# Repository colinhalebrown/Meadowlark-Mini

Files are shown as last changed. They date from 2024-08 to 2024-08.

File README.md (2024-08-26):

# Meadowlark-Mini

Dual deploy programable flight computer for amature rocketry. Equipt with a beeper, physical interrupt, battery charger/monitoring, ignighter indicators, logging to MicroSD, IMU, and Pressure sensor. The goal is to offer a feature rich contnroller that can fit inside a 29mm chassis with the creature comforts of modern controllers. The system is powered by a onboard RP2040 microcontroller. Running at 125MHz with dual core operation for data collection and flight tracking.  

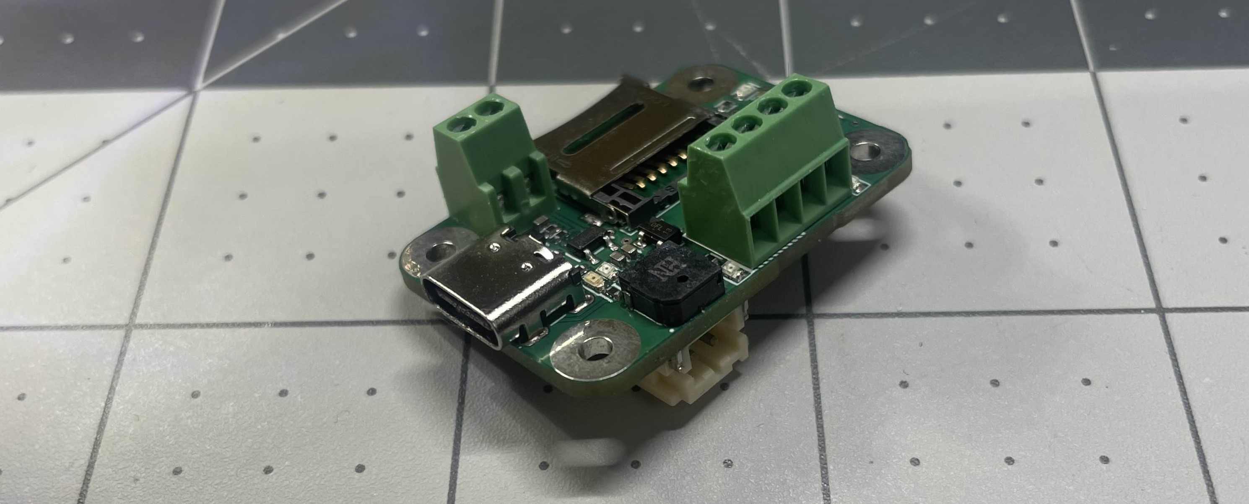
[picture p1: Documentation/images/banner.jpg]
Banner showing PCB


### Hardware Specs
* 260 to 1260 hPa absolute pressure range
* 0.5 hPa absolute pressure accuracy
* +/- 0.025 hPa relative pressure accuracy
* +/- 16g accelerometer range
* +/- 2000 dps gyroscope
* embedded temperature compensation
* 20,000g shock rated
* ~130mA operating consumption 
* Buzzer 80db
* MicroSD data storage

### Hardware Improvements
* add RESET pads for debugging
* move BOOT pads closer together
* Choose different SDcard pins to enable writing code with the picoSDK

### Testing
- [x] Hardware validation
- [x] Firmware Initialized
- [ ] Test Functionallity
        - [x] Indicator light
        - [x] Pyro circuit
        - [x] buzzer
        - [ ] SDcard
        - [ ] Pressure Sensor
        - [ ] IMU
- [ ] Software endurance test
- [ ] Simulated flight test
- [ ] Passeenger flight tests (collect data and tune triggers)
- [ ] Flight as main controller
- [ ] Flight as secondary controller

Repeat any tests until the controller passes with reliable behavior.

# Hardware
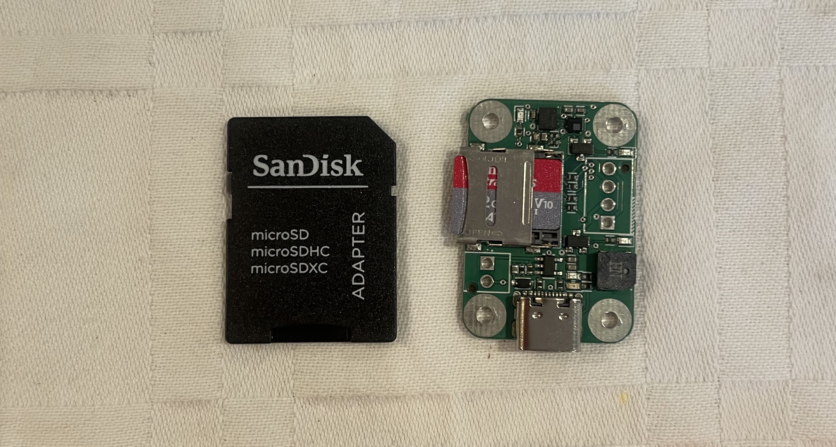
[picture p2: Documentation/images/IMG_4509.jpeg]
PCB size


When designing the board I wanted to a microSD card slot that locks the card into the board. After our push card lock slot ejected the SD card in flight at spaceport I wanted to have a more robust card holder. 

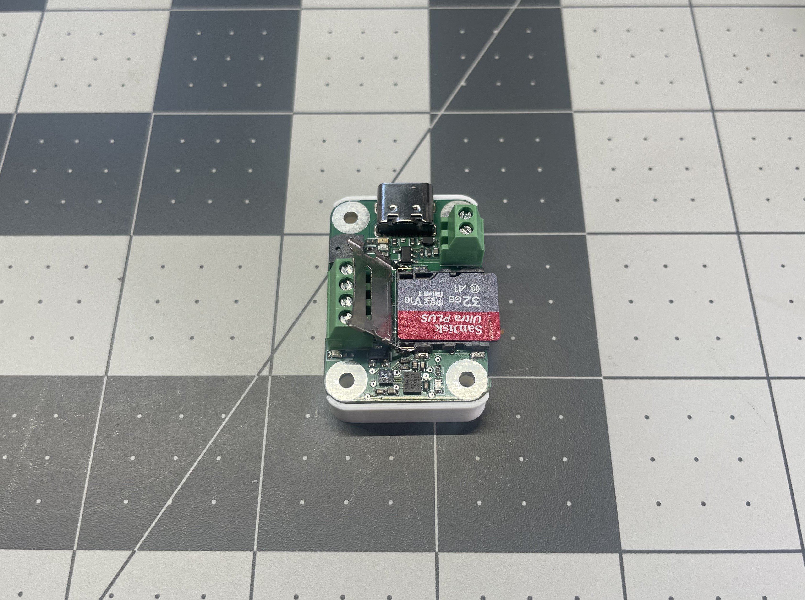
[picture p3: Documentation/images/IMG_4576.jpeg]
PCB MicroSD card Example


The other china specific part that was hard to find was a small buzzer. Getting the board to fit in a 29mm body tube meant I needed to shrink my components as much as possible.

### [Hardware Details](https://github.com/colinhalebrown/Meadowlark-Mini/tree/main/Hardware)

# Software
I started by testing functionality of the controller with the arduino IDE. That worked well however I wanted to shift to using the PICO-SDK with vscode to write softwar with the goal of making the firmware more reliable and more power efficent.

### Pinout
|System |Signal Type |Label| GPIO |Verified|
|---|---|-----|---|---|
|Indicator LED  |Digital Output|D13  |GPIO13|Y |
|Buzzer |Digital Output|A0 |GPIO26|Y |
|Battery Monior |Analog Input  |A1 |AD1 |Y |
|Pyro 1 |Digital Output|D12  |GPIO12|Y |
|Pyro 2 |Digital Output|D4 |GPIO6 |Y |
|Pressure Sensor|I2C |SDA, SCL|GPIO2, GPIO3| |
|IMU |I2C |SDA, SCL  |GPIO2, GPIO3| |
|MicroSD Card |SPI |MISO, MOSI, SCK, D10|GPIO20, GPIO19, GPIO18, GPIO10|Y|

# Status
Currently the system needs more programming and testing. I fried controllers I/O while working with the board so a new RP2040 will need to be soldiered to the board. 

I plan to repair the test article and finish the functionality tests with the existing design using the arduino IDE. I need to update the PCB to develop code using vscode in the future.

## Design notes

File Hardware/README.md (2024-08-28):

# Meadowlark-Mini Hardware

Banner showing PCB

### Known Issues
* Move Boot pads closer together
* Add reset pads for pico-SDK development
* Fix battery connector positive and negative poles are backwards (Swaped connector for testing)

I ordered the PCBs with all of the china only components on one side of the board to to save on shipping and assembly time.

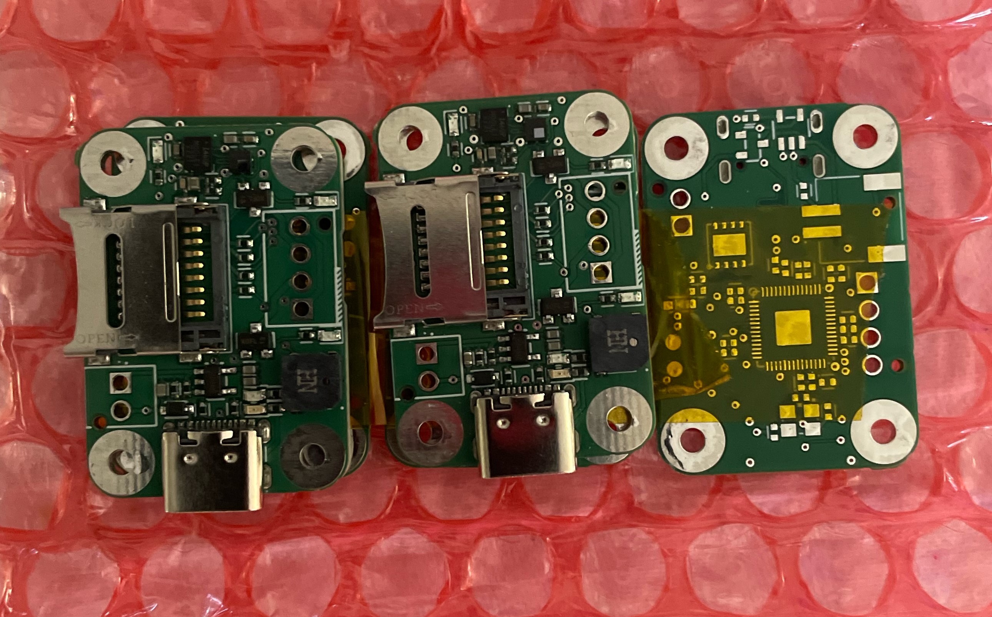
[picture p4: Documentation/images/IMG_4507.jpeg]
PCB on arrival


I then assembled the bottom of the board by hand.

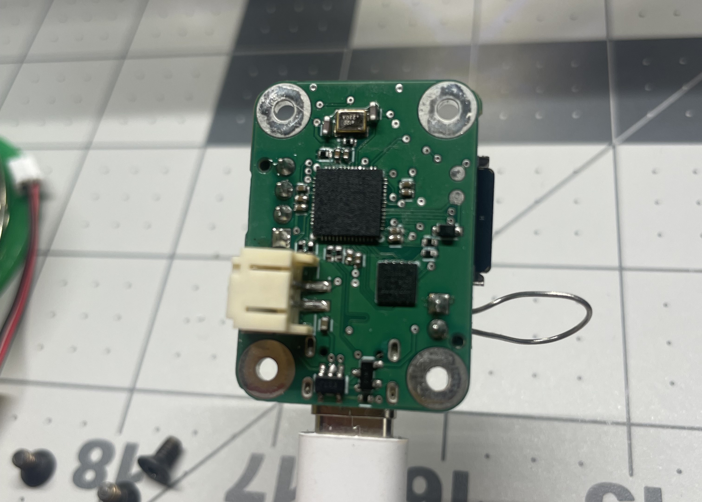
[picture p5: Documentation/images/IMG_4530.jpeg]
Bottom of board


With connectors on both sides of the board and an exposed PCB I wanted to protect the board. I made a two part case that is minimal, acts as a standoff for the board and can lock the microSD card in completely with the top installed. 

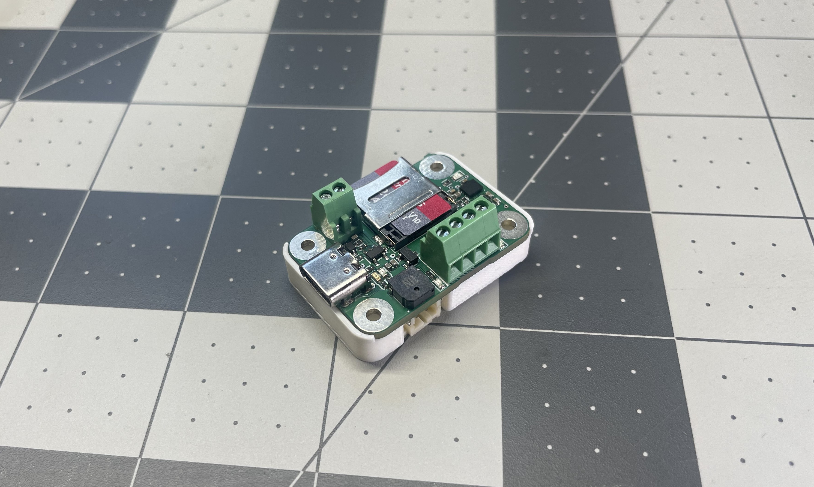
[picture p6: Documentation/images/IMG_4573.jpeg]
PCB bottom case


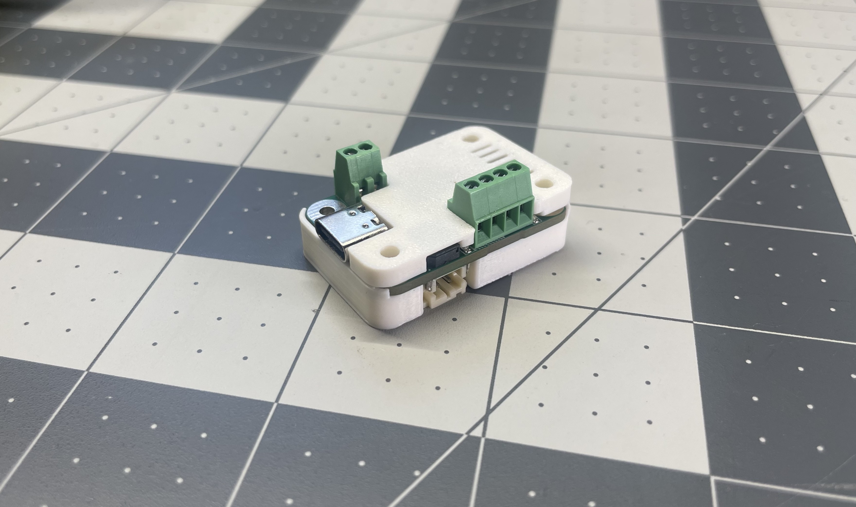
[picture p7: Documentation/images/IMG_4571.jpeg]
PCB top case


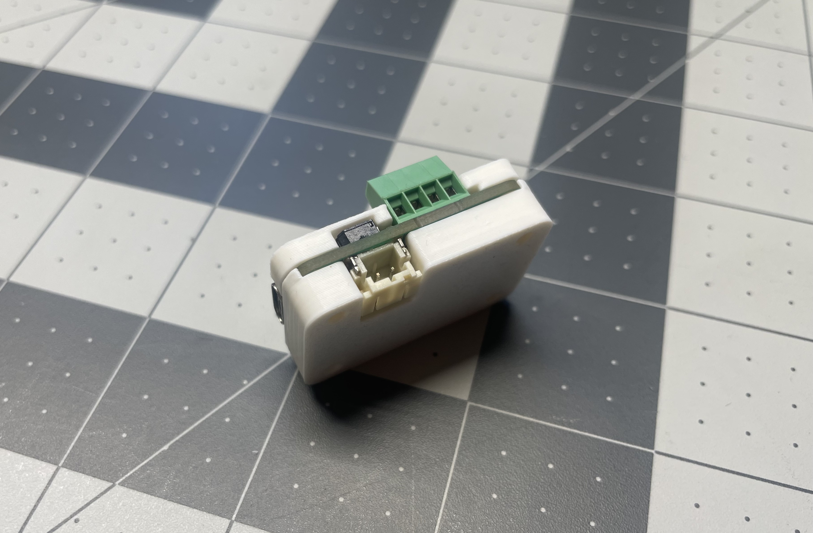
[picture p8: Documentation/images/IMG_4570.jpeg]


The case is designed in two parts, the top is intended to protect the components while not muting the buzzer and allowing the sensors to get fresh air. The bottom of the case brings the battery connector flush to the mounting surface and protects the components on the bottom.

| Top | Bottom |
| --- | --- |
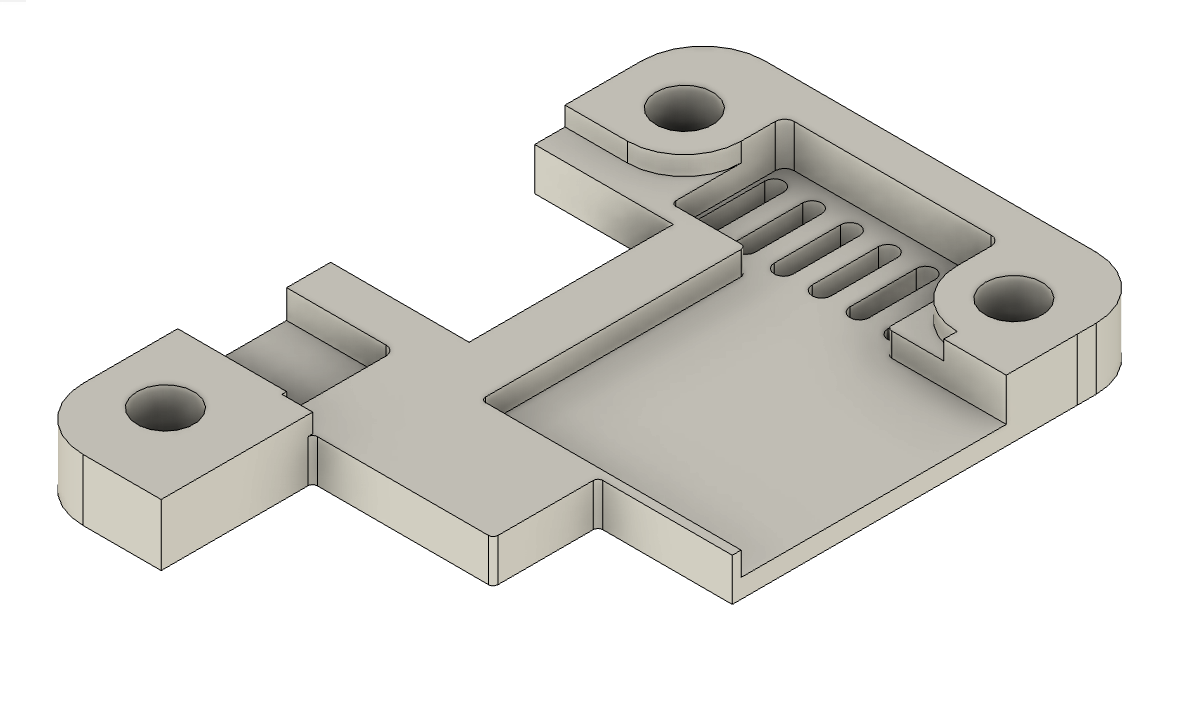
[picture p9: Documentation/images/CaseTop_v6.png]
Top Enclosure
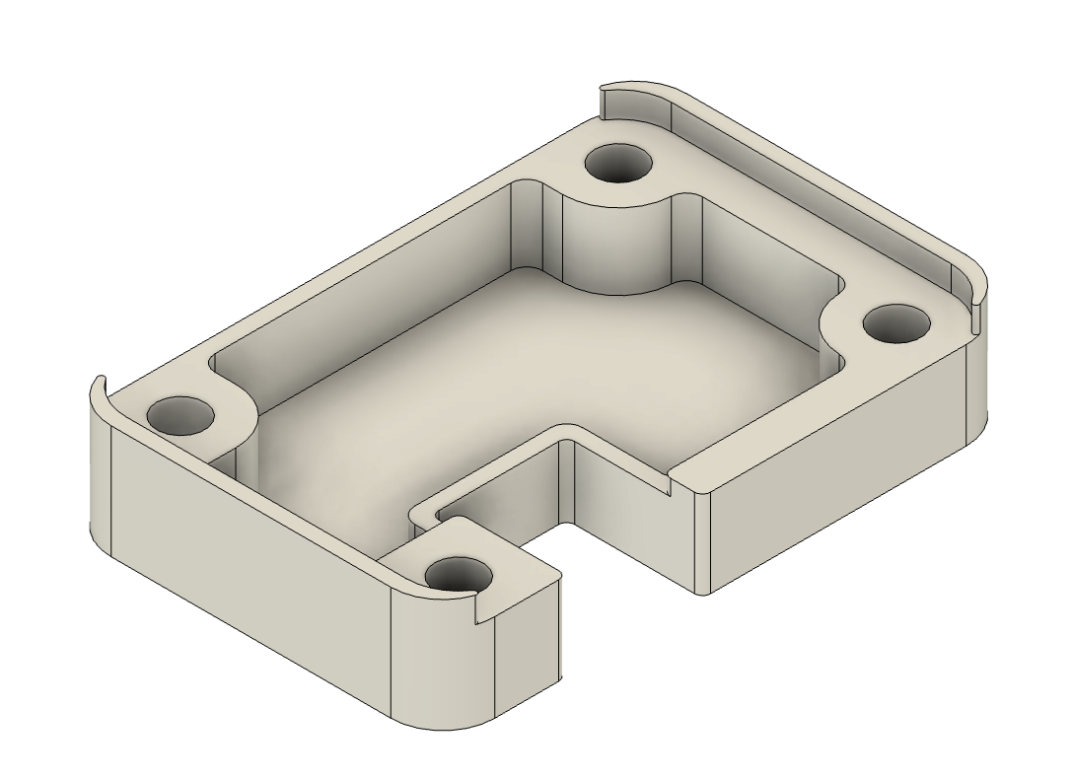
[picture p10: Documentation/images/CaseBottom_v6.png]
Bottom Enclosure
|  |  |

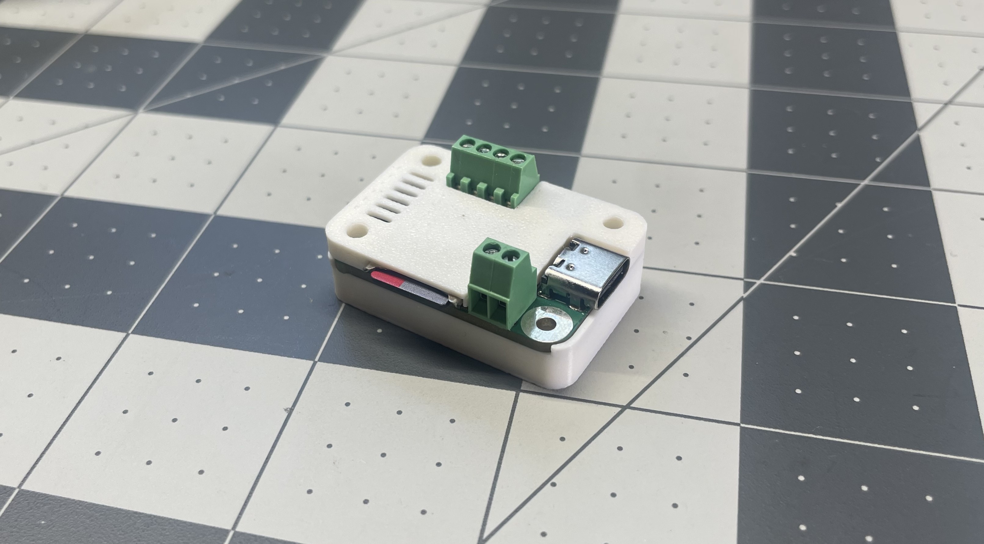
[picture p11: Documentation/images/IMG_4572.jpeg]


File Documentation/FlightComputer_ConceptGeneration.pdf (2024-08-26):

Colin Hale-Brown

Project Goals:
- Low cost
- Easy for users to operate
- Fit in rockets of all sizes
- Lower the barrier to entry for dual deploy rockets

Possible Features:
- Pyro charges (dual or quad)
- L2 or L3 GPS
- Radio
- Data storage
- Audio Cues
- Altimeter
- Gyroscope
- Accelerometer
- Magnetometer
- Voltage monitoring
- External pyro battery
- Battery charger
- STEMMA QT plug
- Ground station
- Verbal cues
- Ground testing
- 29mm rocket diameter

Most fliers want redundant controllers over a single quad charge controller with the thinking being that it is an additional failure mode however that implies that a controller fails to work entirely.

Discussing failure modes with users in the community I found that the backup controller is more there for peace of mind. The most common failures are controllers not powered on, low battery, or incorrectly configured. With the only non-user failures told to me being screws that come loose during flight in the AV bay and damage the exposed electronics or water damage due to high humidity or direct contact with water. While I feel that a single more advanced controller would be a better use of money, users are adamant that they would not fly a controller like that.

With these learnings in mind I wanted to make a simple controller that is capable yet cost effective and small enough to fit in a 29mm rocket. A dual pyro controller makes the most sense because users are going to use two of them anyways. They need to have recoverable data storage so using a microSD card would be ideal. When the device is in the rocket it would be great to know it is operational on the pad using a buzzer of some kind as an audio indicator. The device should have USB-C for charging the li-po powering it and for debugging the system if needed. Because of where we launch and the theme of naming flight computers after birds, I am going to call this controller the Meadowlark Mini.

Colin Hale-Brown

Meadowlark Mini Target Specs:
- Dual mosfet pyro controllers with screw terminals for attaching charges
- Interrupt switch for powering on the system, either JST or screw terminal
- RP2040 microcontroller
- Piezzo buzzer
- USB-C for Li-Po charging and serial communication
- Li-Po connector and power management
- Barometric pressure sensor
- Accelerometer and gyroscope (magnetometer would be cool but not required)
- LEDs for power and status indicators
- M3 mounting locations

I removed any power switches and buttons for the boot loader and board reset from the board to save weight, cost, and prevent failure due to g-forces during flight. Pads for Pogo pins can be found on the bottom of the board for programming and debugging. To prevent water related failures the board can be coated in a conformal coating. To prevent a failure due to loose debris in the AV bay I would like to design a sleek, lightweight case for the board to protect it in flight and when being handled. This also protects the conformal coating from chipping and damage which could lead to water related failures. I would like to get the BOM down below $20 for the flight computer so that a kit for $50 could include an interrupt switch and battery along with the flight computer itself.

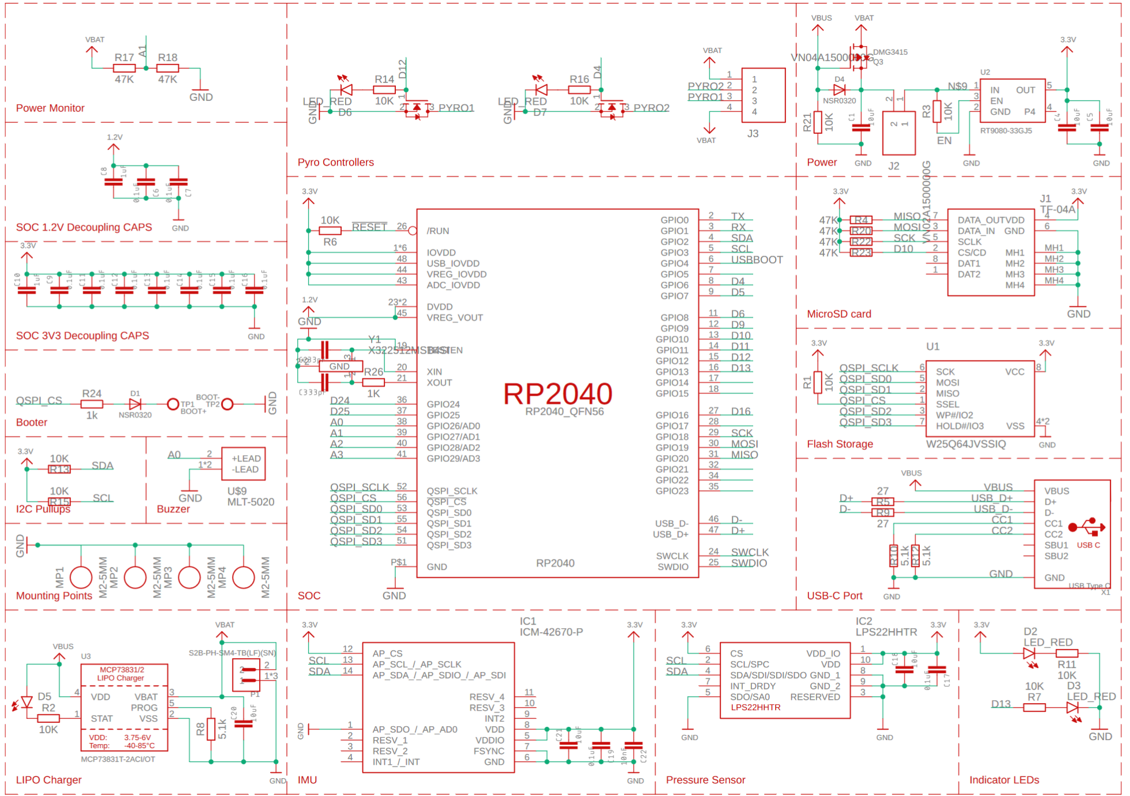
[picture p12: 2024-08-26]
Documentation/images/schematic_v30.png

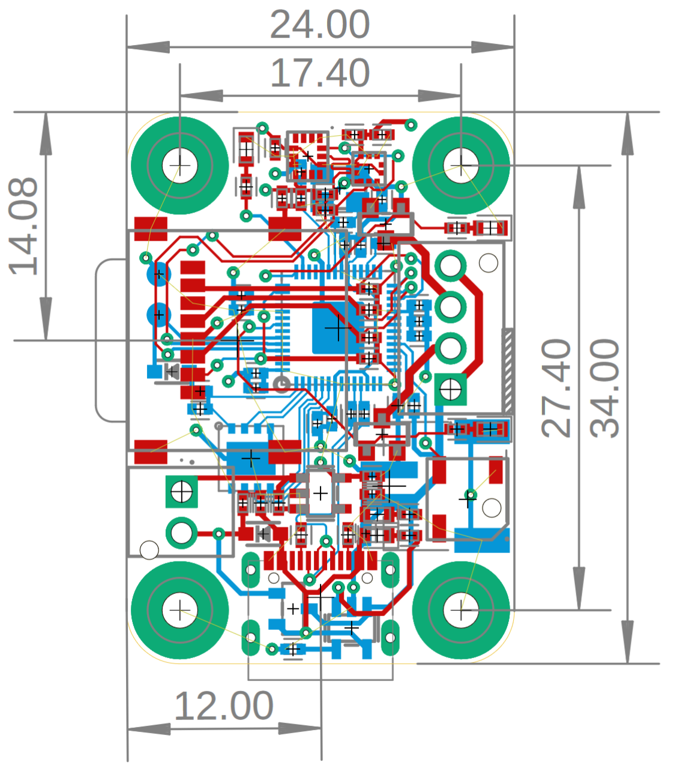
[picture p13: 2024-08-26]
Documentation/images/BoardDimentions_v49.png

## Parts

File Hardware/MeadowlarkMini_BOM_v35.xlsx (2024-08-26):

Meadowlark Mini BOM
Comment | Designator | Footprint | Part # | URL | QTY | Type | Notes
MLT-5020 | U$9 | MLT5020 | C94598 | JLC (https://jlcpcb.com/partdetail/Jiangsu_HuanengElec-MLT5020/C94598) | 1 | Extended | Buzzer
S2B-PH-SM4-TB | P1 | JST_S2B-PH-SM4-TB(LF)(SN) | C295747 | JLC (https://jlcpcb.com/partdetail/Jst-S2B_PH_SM4_TB_LF_SN/C295747) | 1 | Extended | JST-PH 2P
RP2040 | RP2040 | QFN56_7MM_REDUCEDEPAD | C2040 | JLC (https://jlcpcb.com/partdetail/RaspberryPi-RP2040/C2040) | 1 | Extended | RP2040 SOC
TF-04A | J1 | TF04A | C145799 | JLC (https://jlcpcb.com/partdetail/Korean_HropartsElec-TF04A/C145799) | 1 | Extended | MicroSD Slot
DB125-2.54-4P-GN-S | J3 | VN04A1500000G | C918122 | JLC (https://jlcpcb.com/partdetail/Dorabo-DB125_2_54_4P_GNS/C918122) | 1 | Extended | 4P 2.54mm Screw
DB301V-3.5-2P-GN-S | J2 | VN02A1500000G | C918120 | JLC (https://jlcpcb.com/partdetail/Dorabo-DB125_2_54_2P_GNS/C918120) | 1 | Extended | 2P 2.54mm Screw
W25Q64JVXGIQ | U1 | USON8_4X4 | C2940195 | JLC (https://jlcpcb.com/partdetail/WinbondElec-W25Q64JVXGIQ/C2940195) | 1 | Extended | Flash Storage
ICM-42670-P | IC1 | ICM42670P | C3288646 | JLC (https://jlcpcb.com/partdetail/TdkInvensense-ICM_42670P/C3288646) | 1 | Extended | IMU
LPS22HHTR | IC2 | LPS22HHTR | C2827824 | JLC (https://jlcpcb.com/partdetail/Stmicroelectronics-LPS22HHTR/C2827824) | 1 | Extended | Barometer
SI2301CDS-T1-GE3 | Q3 | SOT23-R | C10487 | JLC (https://jlcpcb.com/partdetail/VishayIntertech-SI2301CDS_T1GE3/C10487) | 1 | Basic | Power MOSFET
RT9080-33GJ5 | U2 | SOT23-5 | C841192 | JLC (https://jlcpcb.com/partdetail/RichtekTech-RT908033GJ5/C841192) | 1 | Extended | Voltage regulator
MCP73831T-2ACI/OT | U3 | SOT23-5 | C424093 | JLC (https://jlcpcb.com/partdetail/MicrochipTech-MCP73831T_2ACIOT/C424093) | 1 | Extended | LIPO Charger
TYPE-C 16PIN 2MD(073) | X1 | USB_C_CUSB31-CFM2AX-01-X | C2765186 | JLC (https://jlcpcb.com/partdetail/ShouHan-TYPE_C_16PIN_2MD_073/C2765186) | 1 | Extended | USB-C port
AO3400A | Q1, Q2 | SOT23-WIDE | C20917 | JLC (https://jlcpcb.com/partdetail/Alpha_OmegaSemicon-AO3400A/C20917) | 2 | Basic | Load MOSFET
0402WGF1001TCE | R24, R26 | RESC1005X40 | C11702 | JLC (https://jlcpcb.com/partdetail/12256-0402WGF1001TCE/C11702) | 2 | Basic | 1k 0402
1N5819WS | D1, D4 | SOD-323_MINI | C191023 | JLC (https://jlcpcb.com/partdetail/GuangdongHottech-1N5819WS/C191023) | 2 | Basic | Original Part (https://jlcpcb.com/partdetail/Onsemi-NSR0320MW2T1G/C48192)
0402WGF1002TCE | R1, R2, R3, R6, R7, R11, R13, R14, R15, R16, R21 | RESC1005X40 | C25744 | JLC (https://jlcpcb.com/partdetail/26487-0402WGF1002TCE/C25744) | 13 | Basic | 10k 0402
CL05A106MQ5NUNC | C1, C4, C5, C18, C20, C21 | CAPC1005X60 | C15525 | JLC (https://jlcpcb.com/partdetail/16204-CL05A106MQ5NUNC/C15525) | 6 | Basic | 10uF 0402
CL05B104KB54PNC | C6, C7, C9, C11, C12, C13, C14, C15, C16, C17, C19 | CAPC1005X60 | C307331 | JLC (https://jlcpcb.com/partdetail/291005-CL05B104KB54PNC/C307331) | 11 | Basic | 0.1uF 0402
CL05B103KB5NNNC | C22 | CAPC1005X60 | C15195 | JLC (https://jlcpcb.com/partdetail/15869-CL05B103KB5NNNC/C15195) | 1 | Basic | 10nF 0402
KT-0603R | D2, D3, D6, D7 | LEDC1608X55N_FLAT-R | C2286 | JLC (https://jlcpcb.com/partdetail/Hubei_KentoElec-KT0603R/C2286) | 4 | Basic | Red LED 0603
19-213/Y2C-CQ2R2L/3T(CY) | D5 | LEDC1608X55N_FLAT-Y | C72038 | JLC (https://jlcpcb.com/partdetail/73147-19_213_Y2C_CQ2R2L_3T_CY/C72038) | 1 | Basic | Yellow LED 0603
0402WGF5101TCE | R8, R10, R12 | RESC1005X40 | C25905 | JLC (https://jlcpcb.com/partdetail/26648-0402WGF5101TCE/C25905) | 3 | Basic | 5.1k 0402
0402WGF4702TCE | R4, R17, R18, R20, R22, R23 | RESC1005X40 | C25792 | JLC (https://jlcpcb.com/partdetail/26535-0402WGF4702TCE/C25792) | 6 | Basic | 47k 0402
0402CG330J500NT | C2, C3 | CAPC1005X60 | C1562 | JLC (https://jlcpcb.com/partdetail/1914-0402CG330J500NT/C1562) | 2 | Basic | 33pF 0402
X322512MSB4SI | Y1 | X322512MSB4SI | C9002 | JLC (https://jlcpcb.com/partdetail/Yxc-X322512MSB4SI/C9002) | 1 | Basic | Clock Cystal
CL05A105KA5NQNC | C8, C10 | CAPC1005X60 | C52923 | JLC (https://jlcpcb.com/partdetail/53938-CL05A105KA5NQNC/C52923) | 2 | Basic | 1uF 0402
0402WGF270JTCE | R5, R9 | RESC1005X40 | C25100 | JLC (https://jlcpcb.com/partdetail/25843-0402WGF270JTCE/C25100) | 2 | Extended | 27 0402

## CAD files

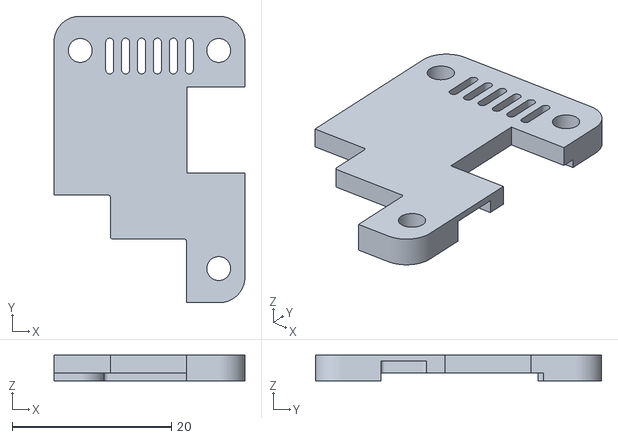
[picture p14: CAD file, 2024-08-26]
Hardware/Case_Top-v6.stl
24.0 x 36.0 x 3.25

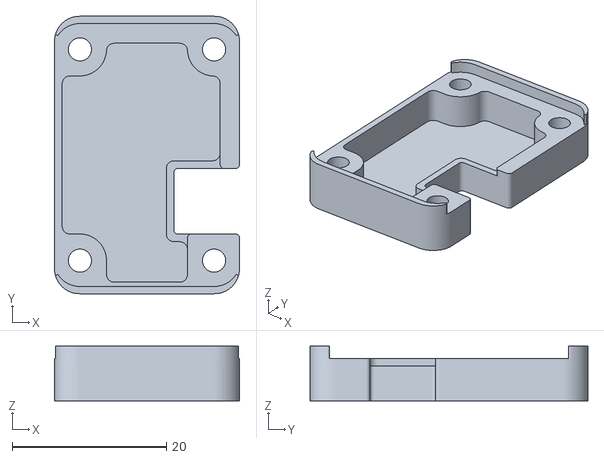
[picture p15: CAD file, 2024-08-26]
Hardware/Case_Bottom-v6.stl
24.0 x 36.0 x 7.10

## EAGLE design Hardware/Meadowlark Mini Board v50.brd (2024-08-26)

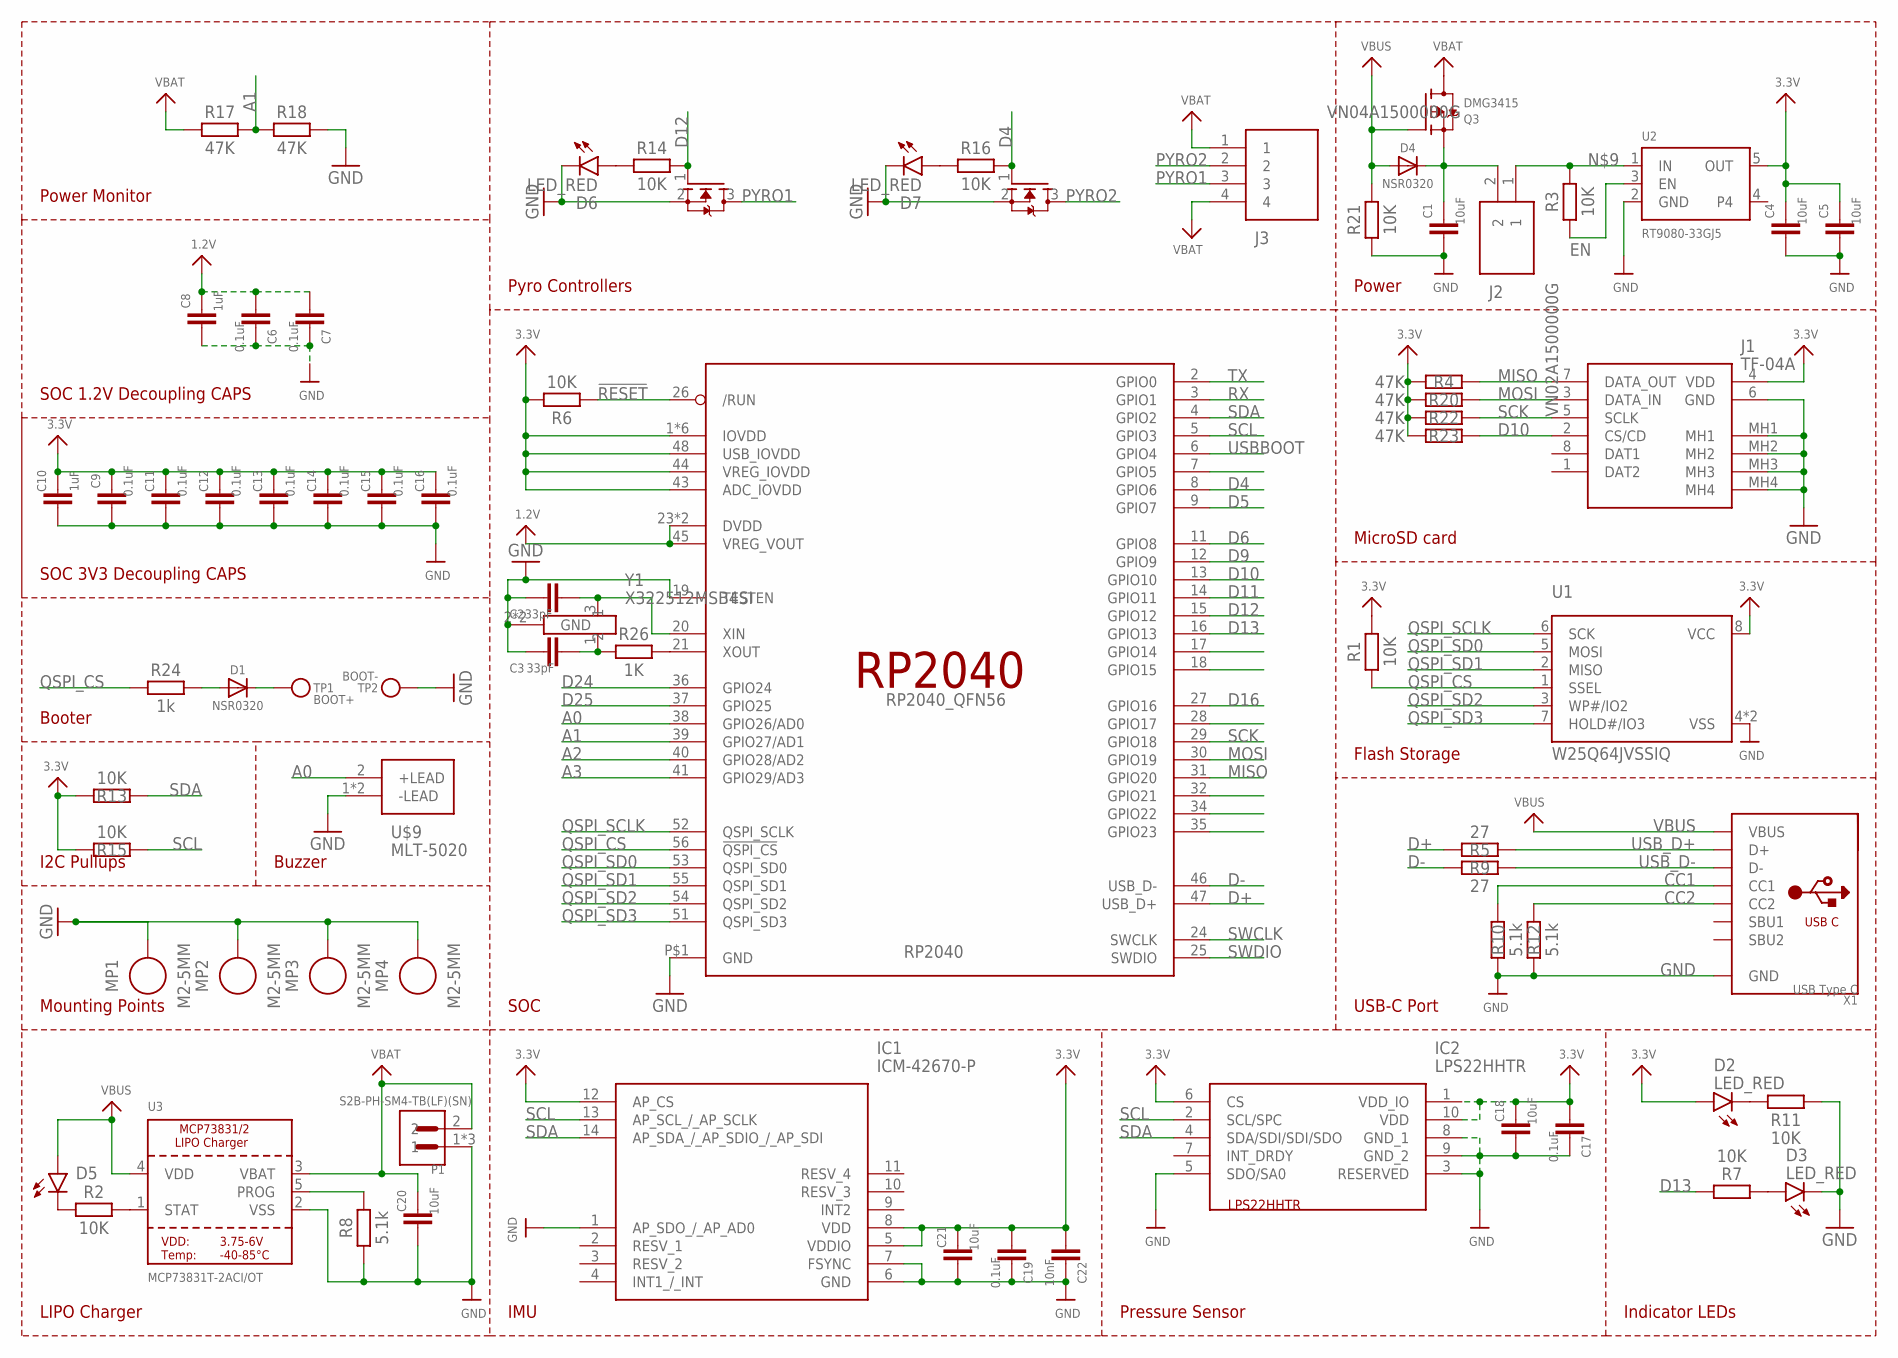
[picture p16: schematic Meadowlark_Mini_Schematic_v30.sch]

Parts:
C1, C4, C5, C18, C20, C21: 10uF; CAPC1005X60
C2, C3: 33pF; CAPC1005X60
C6, C7, C9, C11, C12, C13, C14, C15, C16, C17, C19: 0.1uF; CAPC1005X60
C8, C10: 1uF; CAPC1005X60
C22: 10nF; CAPC1005X60
D1, D4: NSR0320; SOD-323_MINI
D2, D3, D6, D7: LED_RED; LEDC1608X55N_FLAT-R
D5: LED_YELLOW; LEDC1608X55N_FLAT-Y
IC1: ICM-42670-P; ICM42670P
IC2: LPS22HHTR
J1: TF-04A; TF04A
J2: VN02A1500000G
J3: VN04A1500000G
MP1, MP2, MP3, MP4: M2-5MM; STANDOFF_HEX_MALE-FEMALE_400X500_M2X0.4_MTGP600H220
P1: S2B-PH-SM4-TB(LF)(SN); JST_S2B-PH-SM4-TB(LF)(SN)
Q1, Q2: AO3400A; SOT23-WIDE
Q3: DMG3415; SOT23-R
R1, R2, R3, R6, R7, R11, R13, R14, R15, R16, R21: 10K; RESC1005X40
R4, R17, R18, R20, R22, R23: 47K; RESC1005X40
R5, R9: 27; RESC1005X40
R8, R10, R12: 5.1k; RESC1005X40
R24: 1k; RESC1005X40
R26: 1K; RESC1005X40
RP2040: RP2040_QFN56; QFN56_7MM_REDUCEDEPAD
TP1: BOOT+; TESTPOINT_ROUND_1.5MM_NO
TP2: BOOT-; TESTPOINT_ROUND_1.5MM_NO
U1: W25Q64JVSSIQ; USON8_4X4
U2: RT9080-33GJ5; SOT23-5; JLC_ROTATION 0
U3: MCP73831T-2ACI/OT; SOT23-5
U$9: MLT-5020; MLT5020
X1: USB Type C; USB_C_CUSB31-CFM2AX-01-X
Y1: X322512MSB4SI

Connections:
1.2V: C6.2, C7.2, C8.1, RP2040.23 (DVDD), RP2040.45 (VREG_VOUT), RP2040.50 (DVDD)
3.3V: C4.1, C5.1, C9.1, C10.1, C11.1, C12.1, C13.1, C14.1, C15.1, C16.1, C17.2, C18.1, C19.2, C21.1, C22.2, D2.A, IC1.5 (VDDIO), IC1.8 (VDD), IC1.12 (AP_CS), IC2.1 (VDD_IO), IC2.6 (CS), IC2.10 (VDD), J1.4 (VDD), R1.2, R4.1, R6.2, R13.2, R15.2, R20.1, R22.1, R23.1, RP2040.1 (IOVDD), RP2040.10 (IOVDD), RP2040.22 (IOVDD), RP2040.33 (IOVDD), RP2040.42 (IOVDD), RP2040.43 (ADC_IOVDD), RP2040.44 (VREG_IOVDD), RP2040.48 (USB_IOVDD), RP2040.49 (IOVDD), U1.8 (VCC), U2.5 (OUT)
!RESET: R6.1, RP2040.26 (/RUN)
A0: RP2040.38 (GPIO26/AD0), U$9.2 (+LEAD)
A1: R17.2, R18.1, RP2040.39 (GPIO27/AD1)
A2: RP2040.40 (GPIO28/AD2)
A3: RP2040.41 (GPIO29/AD3)
CC1: R10.2, X1.A5 (CC1)
CC2: R12.2, X1.B5 (CC2)
D4: Q2.1 (G), R16.2, RP2040.8 (GPIO6)
D5: RP2040.9 (GPIO7)
D6: RP2040.11 (GPIO8)
D9: RP2040.12 (GPIO9)
D10: J1.2 (CS/CD), R23.2, RP2040.13 (GPIO10)
D11: RP2040.14 (GPIO11)
D12: Q1.1 (G), R14.2, RP2040.15 (GPIO12)
D13: R7.2, RP2040.16 (GPIO13)
D16: RP2040.27 (GPIO16)
D24: RP2040.36 (GPIO24)
D25: RP2040.37 (GPIO25)
D+: R5.1, RP2040.47 (USB_D+)
D-: R9.1, RP2040.46 (USB_D-)
EN: R3.1, U2.3 (EN)
GND: C1.2, C2.1, C3.1, C4.2, C5.2, C6.1, C7.1, C8.2, C9.2, C10.2, C11.2, C12.2, C13.2, C14.2, C15.2, C16.2, C17.1, C18.2, C19.1, C20.2, C21.2, C22.1, D3.C, D6.C, D7.C, IC1.1 (AP_SDO_/_AP_AD0), IC1.6 (GND), IC1.7 (FSYNC), IC2.3 (RESERVED), IC2.5 (SDO/SA0), IC2.8 (GND_1), IC2.9 (GND_2), J1.6 (GND), J1.MH1, J1.MH2, J1.MH3, J1.MH4, MP1.1, MP2.1, MP3.1, MP4.1, P1.1, P1.P1 (1), P1.P2 (1), Q1.2 (S), Q2.2 (S), R8.1, R10.1, R11.2, R12.1, R18.2, R21.1, RP2040.19 (TESTEN), RP2040.P$1 (GND), TP2.P$1, U1.4 (VSS), U1.PAD (VSS), U2.2 (GND), U3.2 (VSS), U$9.1 (-LEAD), U$9.3 (-LEAD), X1.A1B12 (GND), X1.B1A12 (GND), Y1.2 (GND), Y1.4 (GND)
MISO: J1.7 (DATA_OUT), R4.2, RP2040.31 (GPIO20)
MOSI: J1.3 (DATA_IN), R20.2, RP2040.30 (GPIO19)
unnamed: D5.C, R2.1
unnamed: D2.C, R11.1
unnamed: R2.2, U3.1 (STAT)
unnamed: R8.2, U3.5 (PROG)
unnamed: D6.A, R14.1
unnamed: C3.2, R26.1, Y1.1
unnamed: R26.2, RP2040.21 (XOUT)
unnamed: D1.A, R24.2
unnamed: J2.1, R3.2, U2.1 (IN)
unnamed: D3.A, R7.1
unnamed: D7.A, R16.1
unnamed: C2.2, RP2040.20 (XIN), Y1.3 (2)
PYRO1: J3.3, Q1.3 (D)
PYRO2: J3.2, Q2.3 (D)
QSPI_CS: R1.1, R24.1, RP2040.56 (!QSPI_CS), U1.1 (SSEL)
QSPI_SCLK: RP2040.52 (QSPI_SCLK), U1.6 (SCK)
QSPI_SD0: RP2040.53 (QSPI_SD0), U1.5 (MOSI)
QSPI_SD1: RP2040.55 (QSPI_SD1), U1.2 (MISO)
QSPI_SD2: RP2040.54 (QSPI_SD2), U1.3 (WP#/IO2)
QSPI_SD3: RP2040.51 (QSPI_SD3), U1.7 (HOLD#/IO3)
RX: RP2040.3 (GPIO1)
SCK: J1.5 (SCLK), R22.2, RP2040.29 (GPIO18)
SCL: IC1.13 (AP_SCL_/_AP_SCLK), IC2.2 (SCL/SPC), R15.1, RP2040.5 (GPIO3)
SDA: IC1.14 (AP_SDA_/_AP_SDIO_/_AP_SDI), IC2.4 (SDA/SDI/SDI/SDO), R13.1, RP2040.4 (GPIO2)
SWCLK: RP2040.24 (SWCLK)
SWDIO: RP2040.25 (SWDIO)
TX: RP2040.2 (GPIO0)
USBBOOT: D1.C, RP2040.6 (GPIO4), TP1.P$1
USB_D+: R5.2, X1.A6 (D+), X1.B6 (D+)
USB_D-: R9.2, X1.A7 (D-), X1.B7 (D-)
VBAT: C20.1, J3.1, J3.4, P1.2, Q3.3 (D), R17.1, U3.3 (VBAT)
VBUS: D4.A, D5.A, Q3.1 (G), R21.2, U3.4 (VDD), X1.A4B9 (VBUS), X1.B4A9 (VBUS)
VHI: C1.1, D4.C, J2.2, Q3.2 (S)

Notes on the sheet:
Power
LIPO Charger
MicroSD card
Flash Storage
USB-C Port
SOC
Pyro Controllers
IMU
Pressure Sensor
I2C Pullups
Indicator LEDs
Mounting Points
Buzzer
Booter
SOC 3V3 Decoupling CAPS
SOC 1.2V Decoupling CAPS
Power Monitor

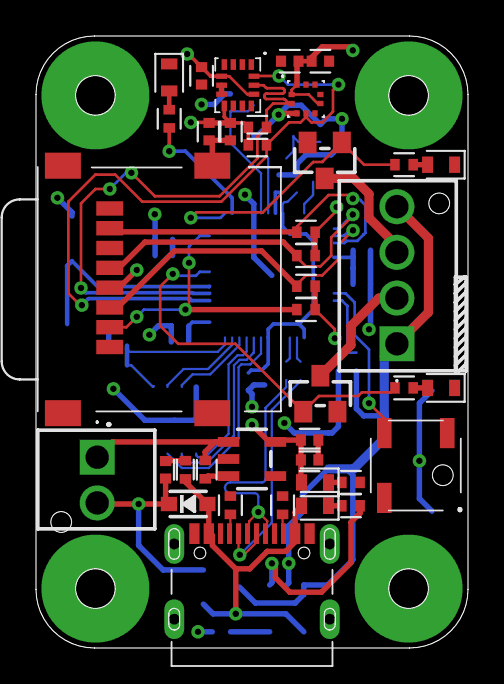
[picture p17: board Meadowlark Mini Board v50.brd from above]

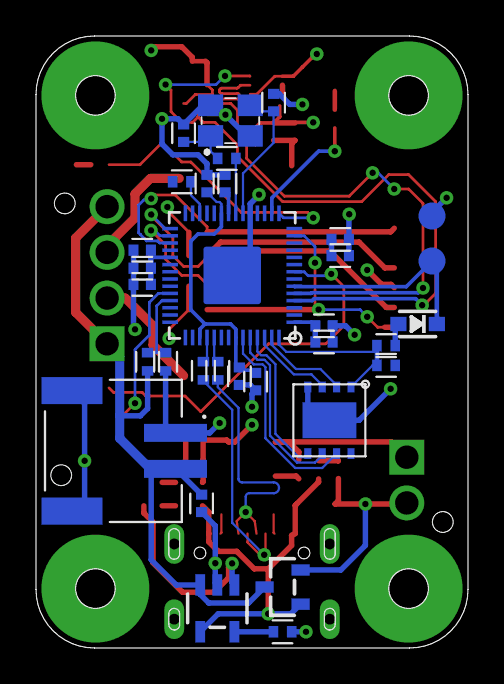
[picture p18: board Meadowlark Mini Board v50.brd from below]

Board: 2 copper layers, 24.0 x 34.0 mm, 75 parts (32 on the bottom side), 46 nets.

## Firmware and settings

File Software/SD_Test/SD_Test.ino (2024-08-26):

/*
  SD card test

  This example shows how use the utility libraries on which the'
  SD library is based in order to get info about your SD card.
  Very useful for testing a card when you're not sure whether its working or not.

  The circuit:
    SD card attached to SPI bus as follows on RP2040:
   ************ SPI0 ************
   ** MISO (AKA RX) - pin 0, 4, or 16
   ** MOSI (AKA TX) - pin 3, 7, or 19
   ** CS            - pin 1, 5, or 17
   ** SCK           - pin 2, 6, or 18
   ************ SPI1 ************
   ** MISO (AKA RX) - pin  8 or 12
   ** MOSI (AKA TX) - pin 11 or 15
   ** CS            - pin  9 or 13
   ** SCK           - pin 10 or 14

  created  28 Mar 2011
  by Limor Fried
  modified 9 Apr 2012
  by Tom Igoe
  modified 26 Dec 2023
  by Richard Teel from code provided by Renzo Mischianti
    SOURCE: https://mischianti.org/raspberry-pi-pico-and-rp2040-boards-how-to-use-sd-card-5/
*/

// This are GP pins for SPI0 on the Raspberry Pi Pico board, and connect
// to different *board* level pinouts.  Check the PCB while wiring.
// Only certain pins can be used by the SPI hardware, so if you change
// these be sure they are legal or the program will crash.
// See: https://datasheets.raspberrypi.com/picow/PicoW-A4-Pinout.pdf
const int _MISO = 8;  // AKA SPI RX
const int _MOSI = 11;  // AKA SPI TX
const int _CS = 9;
const int _SCK = 10;

// include the SD library:
#include <SPI.h>
#include <SD.h>

File root;

void setup() {
  // Open serial communications and wait for port to open:
  Serial.begin(115200);

  while (!Serial) {
    delay(1);  // wait for serial port to connect. Needed for native USB port only
  }

  Serial.println("\nInitializing SD card...");

  bool sdInitialized = false;
  // Ensure the SPI pinout the SD card is connected to is configured properly
  // Select the correct SPI based on _MISO pin for the RP2040
  if (_MISO == 0 || _MISO == 4 || _MISO == 16) {
    SPI.setRX(_MISO);
    SPI.setTX(_MOSI);
    SPI.setSCK(_SCK);
    sdInitialized = SD.begin(_CS);
  } else if (_MISO == 8 || _MISO == 12) {
    SPI1.setRX(_MISO);
    SPI1.setTX(_MOSI);
    SPI1.setSCK(_SCK);
    sdInitialized = SD.begin(_CS, SPI1);
  } else {
    Serial.println(F("ERROR: Unknown SPI Configuration"));
    return;
  }

  if (!sdInitialized) {
    Serial.println("initialization failed. Things to check:");
    Serial.println("* is a card inserted?");
    Serial.println("* is your wiring correct?");
    Serial.println("* did you change the chipSelect pin to match your shield or module?");
    return;
  } else {
    Serial.println("Wiring is correct and a card is present.");
  }
  // 0 - SD V1, 1 - SD V2, or 3 - SDHC/SDXC
  // print the type of card
  Serial.println();
  Serial.print("Card type:         ");
  switch (SD.type()) {
    case 0:
      Serial.println("SD1");
      break;
    case 1:
      Serial.println("SD2");
      break;
    case 3:
      Serial.println("SDHC/SDXC");
      break;
    default:
      Serial.println("Unknown");
  }

  Serial.print("Cluster size:          ");
  Serial.println(SD.clusterSize());
  Serial.print("Blocks x Cluster:  ");
  Serial.println(SD.blocksPerCluster());
  Serial.print("Blocks size:  ");
  Serial.println(SD.blockSize());

  Serial.print("Total Blocks:      ");
  Serial.println(SD.totalBlocks());
  Serial.println();

  Serial.print("Total Cluster:      ");
  Serial.println(SD.totalClusters());
  Serial.println();

  // print the type and size of the first FAT-type volume
  uint32_t volumesize;
  Serial.print("Volume type is:    FAT");
  Serial.println(SD.fatType(), DEC);

  volumesize = SD.totalClusters();
  volumesize *= SD.clusterSize();
  volumesize /= 1000;
  Serial.print("Volume size (Kb):  ");
  Serial.println(volumesize);
  Serial.print("Volume size (Mb):  ");
  volumesize /= 1024;
  Serial.println(volumesize);
  Serial.print("Volume size (Gb):  ");
  Serial.println((float)volumesize / 1024.0);

  Serial.print("Card size:  ");
  Serial.println((float)SD.size() / 1000);

  FSInfo fs_info;
  SDFS.info(fs_info);

  Serial.print("Total bytes: ");
  Serial.println(fs_info.totalBytes);

  Serial.print("Used bytes: ");
  Serial.println(fs_info.usedBytes);

  root = SD.open("/");
  printDirectory(root, 0);
}

void loop(void) {
  // nothing happens after setup finishes.
}

void printDirectory(File dir, int numTabs) {
  while (true) {

    File entry = dir.openNextFile();
    if (!entry) {
      // no more files
      break;
    }
    for (uint8_t i = 0; i < numTabs; i++) {
      Serial.print('\t');
    }
    Serial.print(entry.name());
    if (entry.isDirectory()) {
      Serial.println("/");
      printDirectory(entry, numTabs + 1);
    } else {
      // files have sizes, directories do not
      Serial.print("\t\t");
      Serial.print(entry.size(), DEC);
      time_t cr = entry.getCreationTime();
      time_t lw = entry.getLastWrite();
      struct tm* tmstruct = localtime(&cr);
      Serial.printf("\tCREATION: %d-%02d-%02d %02d:%02d:%02d", (tmstruct->tm_year) + 1900, (tmstruct->tm_mon) + 1, tmstruct->tm_mday, tmstruct->tm_hour, tmstruct->tm_min, tmstruct->tm_sec);
      tmstruct = localtime(&lw);
      Serial.printf("\tLAST WRITE: %d-%02d-%02d %02d:%02d:%02d\n", (tmstruct->tm_year) + 1900, (tmstruct->tm_mon) + 1, tmstruct->tm_mday, tmstruct->tm_hour, tmstruct->tm_min, tmstruct->tm_sec);
    }
    entry.close();
  }
}

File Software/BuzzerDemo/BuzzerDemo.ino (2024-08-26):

/* Arduino tutorial - Buzzer / Piezo Speaker
   More info and circuit: http://www.ardumotive.com/how-to-use-a-buzzer-en.html
   Dev: Michalis Vasilakis // Date: 9/6/2015 // www.ardumotive.com */

const int buzzer = 26;  //buzzer to arduino pin 9

void setup() {
  pinMode(buzzer, OUTPUT);  // Set buzzer - pin 9 as an output
}

void loop() {
  tone(buzzer, 4000);  // Send 1KHz sound signal...
  delay(1000);         // ...for 1 sec
  noTone(buzzer);      // Stop sound...
  delay(1000);         // ...for 1sec
}

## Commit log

2024-08-26 Add content
    [Meadowlark Mini Board v50.brd, MeadowlarkMini_BOM_v35.xlsx, Meadowlark_Mini_Schematic_v30.sch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]
2024-08-26 upload content
    [Case_Bottom-v6.stl, Case_Top-v6.stl]

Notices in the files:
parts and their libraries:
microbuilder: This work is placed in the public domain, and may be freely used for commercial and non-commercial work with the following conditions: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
